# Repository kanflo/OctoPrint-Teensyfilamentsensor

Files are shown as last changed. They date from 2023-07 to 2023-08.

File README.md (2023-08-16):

# OctoPrint Teensy Filament Sensor

Work In Progress!

I wanted a filement sensor for my Duplicator 6 prompted by an "abnormal filament despooling incident". I found the "Smart Filament Sensor" by Bigtreetech, reasonably priced around 25 Euros, but it cannot be connected to the D6. I did have an old [Teensy 2.0](https://www.pjrc.com/teensy/) which could interface the filent sensor. An OctoPring plugin could then monitor the printing process, query the Teensy and act if the filament seemed to have run out or gotten jammed. Obviosly, this "Teensy Smart Filament Sensor" will work for any 3D printer.

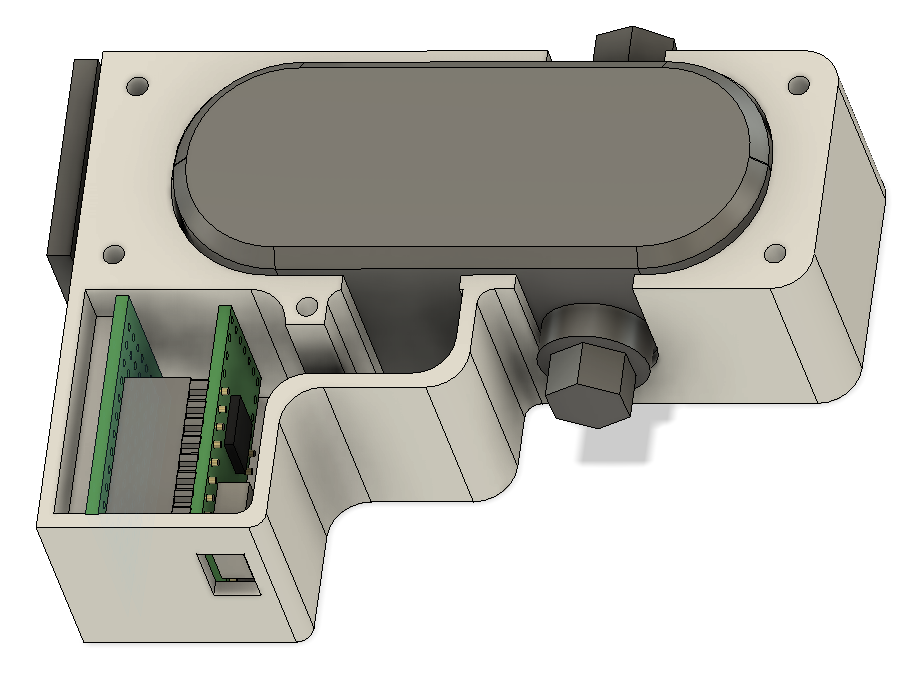
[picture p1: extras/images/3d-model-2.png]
3D Model


## Setup

Install via the bundled [Plugin Manager](https://docs.octoprint.org/en/master/bundledplugins/pluginmanager.html) or manually using this URL:

    https://github.com/kanflo/OctoPrint-Teensyfilamentsensor/archive/master.zip

## Teensy 2.0 firmware

The firmware for the Teensy implements a USB device talking RAW HID, meaning there is no need for a driver. Flash the Teensy with `filamentsensor.hex` or roll your own firmware.

## Mounting

I designed a housing the the filament sensor and Teensy that mounts nicely on the Duplicator 6. I printed them in PLA with 80% infill for sturdiness, probably overkill. Make sure you can insert the "lock peg" into the slot of the "back shell". Also "pre thread" all holes, especially the M4 holes in the lock peg and the corresponding holes in the back shell.

Material needed is:

 - 1x strip board, 9x11 holes
 - 2x Female headers 1x8 (or atleast 1x6)
 - 3x Male headers 1x1
 - 5x M3x8 screws
 - 2x M3 nuts
 - 2x M4x15 screws
 - 2x M4 nuts

1. First solder the headers to the strip board leaving one row of pins on the outside of the Teensy.
2. Solder three male single pin headers for VCC, GND and PF6.
3. Depending on you strip board, make sure the traces are cut, isolating the pins of the Teensy
4. The strip board is fastened by a pair of M3 screws and you need to drill holes in the strip board. Place in inside the 3D printed housing and mark the centers with a pen. Drill both holes.
5. Fasten the two M3 screws with a blob of hot glue or inserting the screw will be difficult. It should now look something like this:

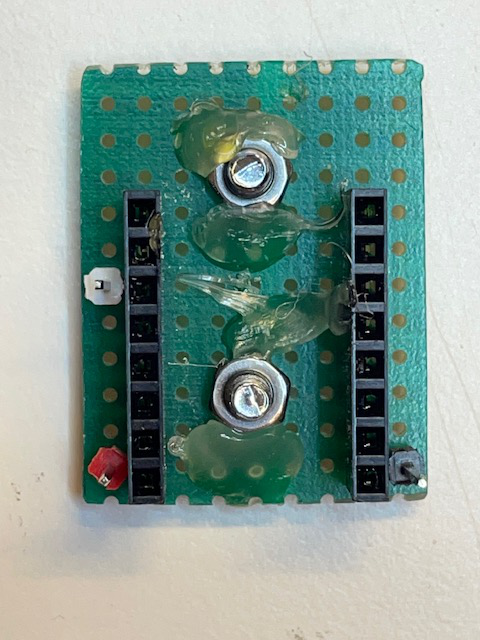
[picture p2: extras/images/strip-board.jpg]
Strip Board


6. Cut the wires fo the filament sensor to about 6cm in length and solder to the three headers. The wires on mine were marked with dense dots (VCC, red), stripes (GND, black) and sparse dots (S, white):

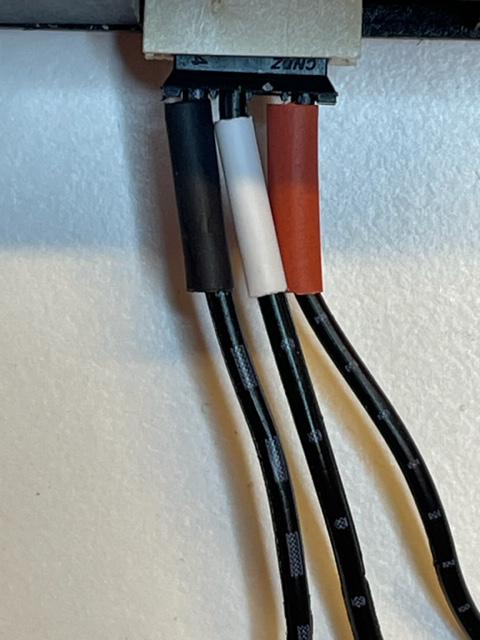
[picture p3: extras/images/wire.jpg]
Filament Sensor Wire


7. Connect the filament sensor to the Teensy, place everything in the housing:

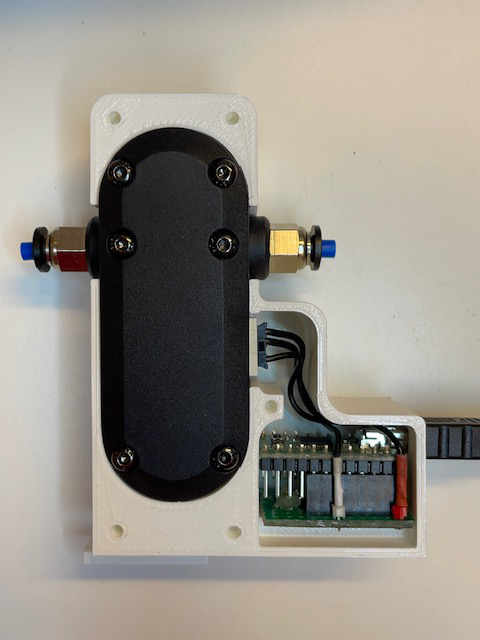
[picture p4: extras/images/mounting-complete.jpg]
Mounting Complete!


8. Depending on your filament sensor, you might need to crack it open and cut the spring inside. Mine was so stiff the extruder failed to pull the filament through the sensor. I took two pair of pliers and pulled the spring and then cut away pieces or it until it was looes enough. I am not sure if it helps, but this is the amount of material I removed:

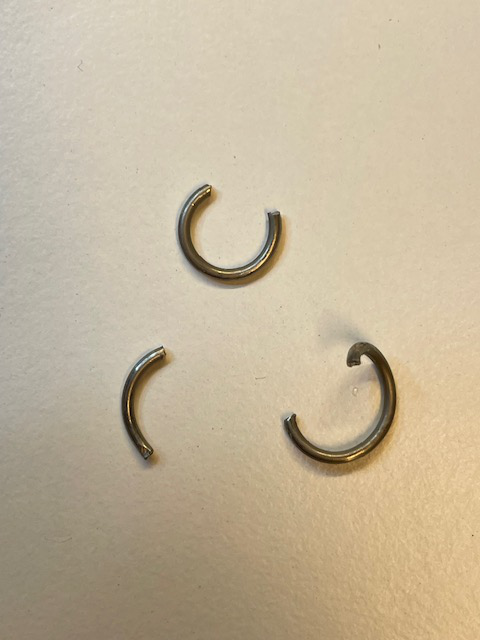
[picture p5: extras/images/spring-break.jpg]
Spring Break


9. Now it's time to mount the sensor. I removed the top holder for the extruder cable to gain access to the mounting hole:

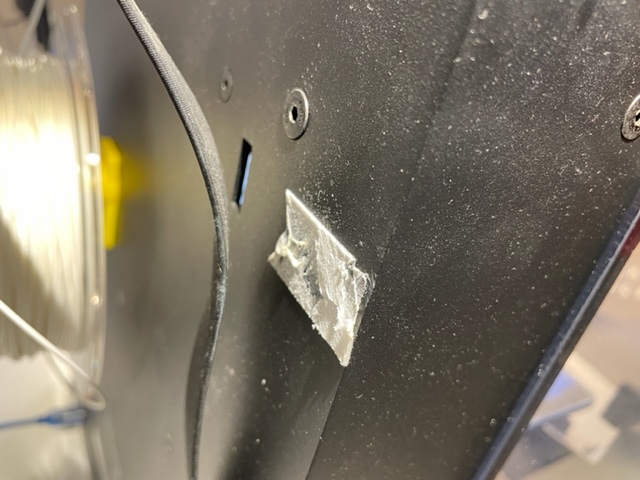
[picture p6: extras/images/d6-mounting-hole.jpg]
D6 Mounting Hole


10. Press the "lock peg" through the hole of the D6, press the housing with the sensor and everything against the lock peg and realize you need one more hand for fastening the M4 screws. I honestly have no idea how I did ut, but succeeded with only two hands ;)

11. Fasten the M4 screws. I had a bit of wiggle so I added some double sided tape between the D6 back wall and the housing.

12. Insert the filement tube into the top of the filement sensor and feed your filament through it:

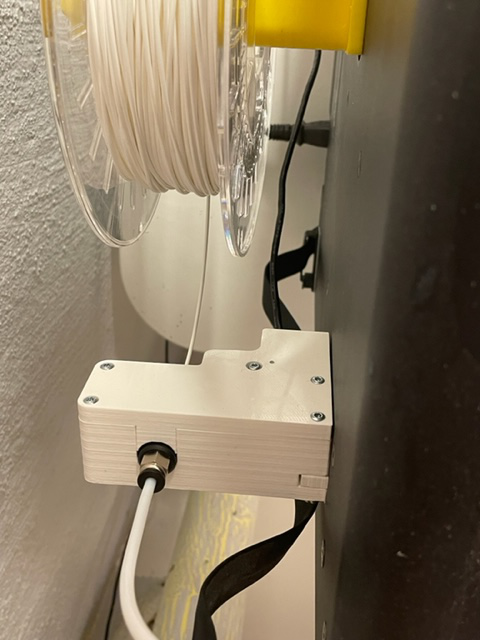
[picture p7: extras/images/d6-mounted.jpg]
Everything Mounted


## Using the filament sensor

Before using the sensor you need to copy a file to your OctoPrint installation. This requires that you know how to connect to your OctoPrint server using SSH:

```
scp extras/00-filament-sensor.rules octopi:
ssh octopi
sudo mv 00-filament-sensor.rules /etc/udev/rules.d
```

If you already connected the Teensy, disconnect and reconnect it.

The plugin adds a status icon to the top bar of the OctoPrint UI:

Filament status in OctoPrint

When the printer is idle, the icon will flash red/gray if the Teensy is disconnected and start flashing green/gray once the Teensy is connected. It should flash green/gray now. If not, ssh to your OctoPrint server and run the command `tail -f logs/octoprint.log`. The directory `logs` is located in a directory called `.octoprint` on my OctoPi.

When printing, the icon will be bright green when the filament status is ok. If the sensor detects a jam, it will light bright red and the print will be stopped (well, that's a TODO for now). If there is an error talking to the Teensy, or if the Teensy is disconnected when printing, the icon will flash bright red/gray.

When the counter ticks, the new counter will be written to the OctoPrint log.

## Configuration

Currently none.

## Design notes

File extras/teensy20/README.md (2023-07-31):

# Teensy 2.0 firmware for the filament sensor

For the impatient, flash `filementsensor.hex` to your Teensy 2.0 using the [https://www.pjrc.com/teensy/loader.html](Teensy loader). Any other Teensy will of course do, I used this 13 year little gem as I had one lying around. If you are patient, install `sudo apt install gcc-avr binutils-avr avr-libc` and run `make`.

Once flashed, you will see a RAW HID device with PID 0x04c9 and VID 0x1234 (I stole the PID from AT&T Microelectronics). Using RAW HID instead of a regular serial port makes you not connect OctoPrint to the filament sensor thinking it is your 3D printer ;)

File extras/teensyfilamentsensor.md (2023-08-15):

---
layout: plugin

id: teensyfilamentsensor
title: OctoPrint-Teensyfilamentsensor
description: A Teensy based filament sensor using Bigtreetech's 'Smart Filament Sensor'. Halts the print in case of filement runout or jam.
authors:
- Johan Kanflo
license: AGPLv3

# TODO
date: 2023-07-31

homepage: https://github.com/kanflo/OctoPrint-Teensyfilamentsensor
source: https://github.com/kanflo/OctoPrint-Teensyfilamentsensor
archive: https://github.com/kanflo/OctoPrint-Teensyfilamentsensor/archive/master.zip

# TODO
# Set this to true if your plugin uses the dependency_links setup parameter to include
# library versions not yet published on PyPi. SHOULD ONLY BE USED IF THERE IS NO OTHER OPTION!
#follow_dependency_links: false

# TODO
tags:
- filement
- sensor

# TODO
# When registering a plugin on plugins.octoprint.org, all screenshots should be uploaded not linked from external sites.
screenshots:
- url: extras/images/octoprint-status.png
  alt: OctoPrint Filement Status
  caption: OctoPrint Filement Status

featuredimage: /extras/images/smart-filament-sensor.png

# TODO
# You only need the following if your plugin requires specific OctoPrint versions or
# specific operating systems to function - you can safely remove the whole
# "compatibility" block if this is not the case.

compatibility:

  # List of compatible versions
  #
  # A single version number will be interpretated as a minimum version requirement,
  # e.g. "1.3.1" will show the plugin as compatible to OctoPrint versions 1.3.1 and up.
  # More sophisticated version requirements can be modelled too by using PEP440
  # compatible version specifiers.
  #
  # You can also remove the whole "octoprint" block. Removing it will default to all
  # OctoPrint versions being supported.

  octoprint:
  - 1.4.0

  # List of compatible operating systems
  #
  # Valid values:
  #
  # - windows
  # - linux
  # - macos
  # - freebsd
  #
  # There are also two OS groups defined that get expanded on usage:
  #
  # - posix: linux, macos and freebsd
  # - nix: linux and freebsd
  #
  # You can also remove the whole "os" block. Removing it will default to all
  # operating systems being supported.

  os:
  - linux
  - windows
  - macos
  - freebsd

  # Compatible Python version
  #
  # It is recommended to only support Python 3 for new plugins, in which case this should be ">=3,<4"
  #
  # Plugins that wish to support both Python 2 and 3 should set it to ">=2.7,<4".
  #
  # Plugins that only support Python 2 will not be accepted into the plugin repository.

  python: ">=3,<4"

---

This is a plugin that talks to a microcontroller interfacing a "Smart Filament Sensor" from Bigtreetech. Currently a Teensy 2.0 is used but any microcontroller will do. The result is a filement sensor that works on any 3D printer.

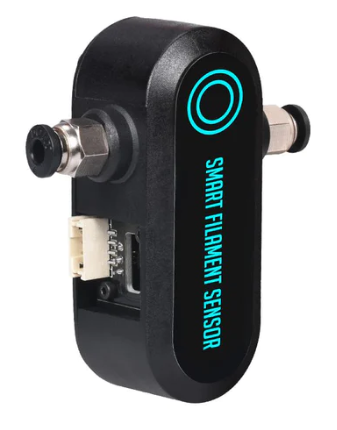
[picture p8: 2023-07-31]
extras/images/smart-filament-sensor.png

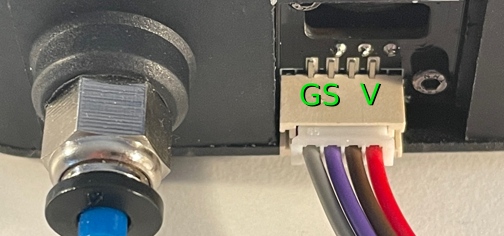
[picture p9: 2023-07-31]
extras/images/smart-filement-sensor-pinut.png

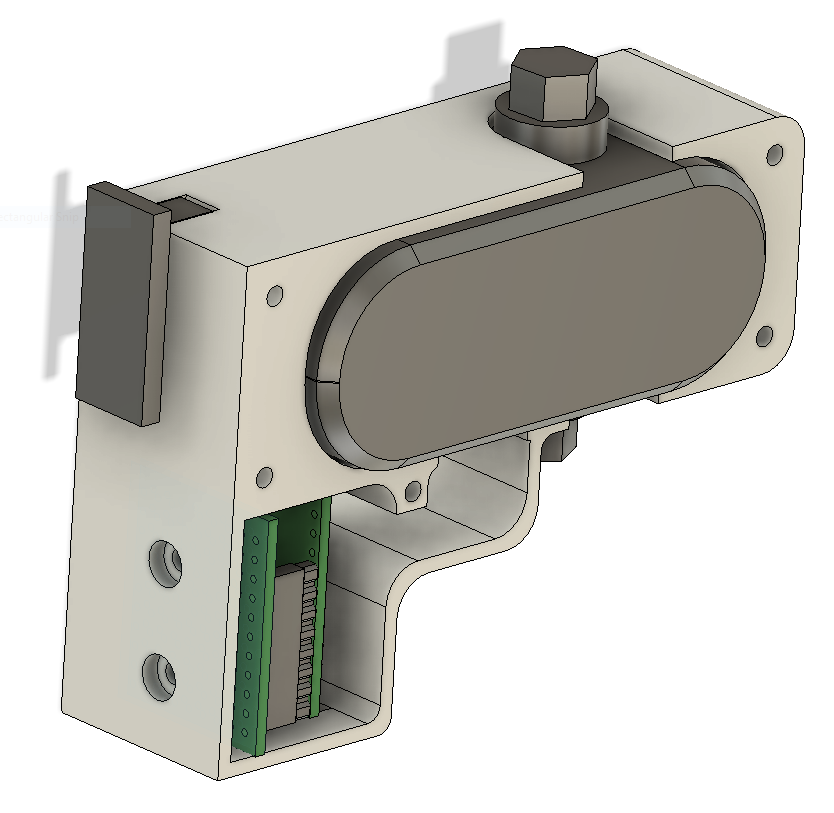
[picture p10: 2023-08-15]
extras/images/3d-model-1.png

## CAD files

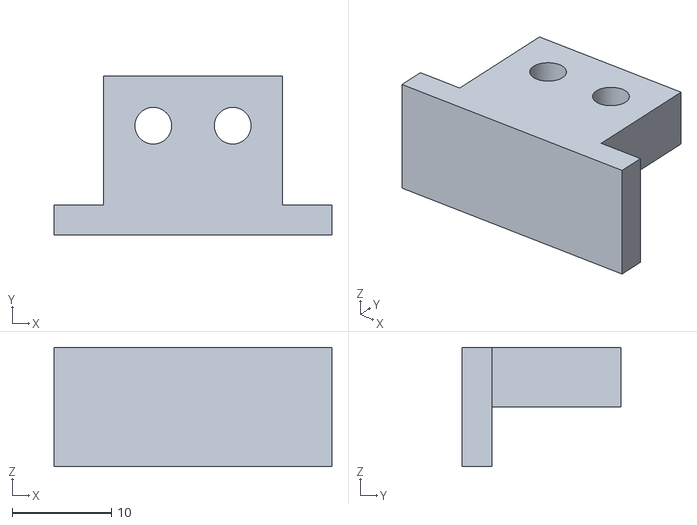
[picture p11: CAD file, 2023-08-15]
extras/stl/Lock Peg v5.stl
28.0 x 16.0 x 12.0

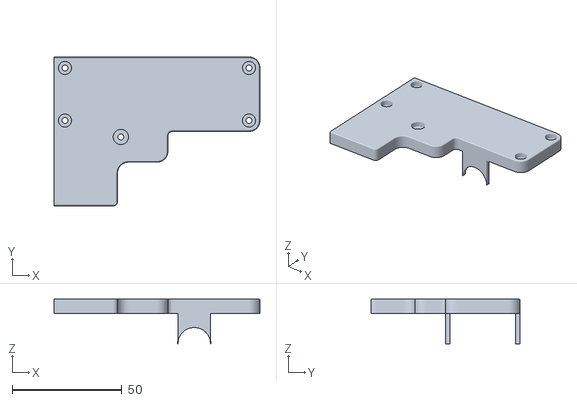
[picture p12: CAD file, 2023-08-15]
extras/stl/Top Shell v19.stl
94.0 x 68.0 x 20.5

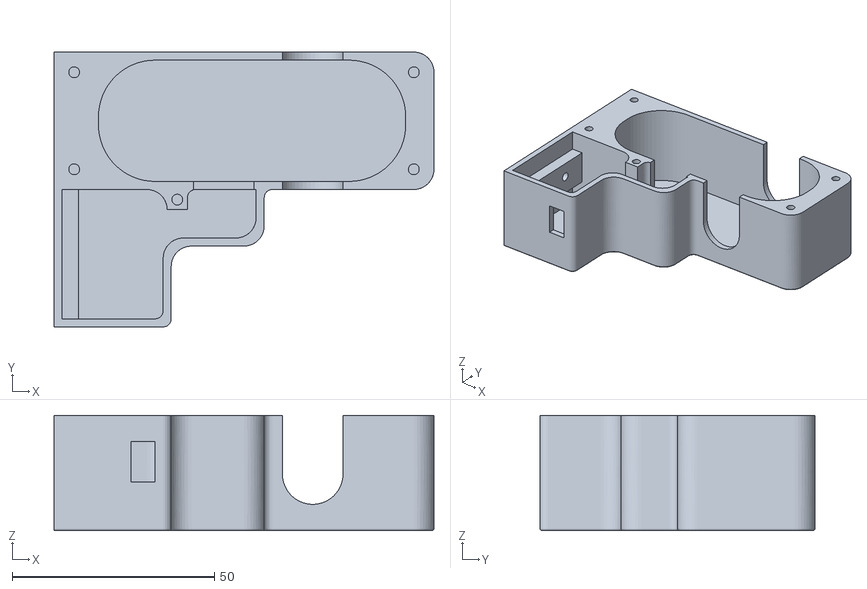
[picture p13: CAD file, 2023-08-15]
extras/stl/Back Shell v26.stl
94.0 x 68.0 x 28.5

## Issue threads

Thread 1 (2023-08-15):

Implement printer stop

kanflo, 2023-08-15:
Currently, the plugin only logs the sensor counter at start of printing and when printing finishes. Investigate how much (or little) filament move is considered normal and implement print stop.

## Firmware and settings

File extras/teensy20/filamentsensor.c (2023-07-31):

/*
 * Copyright (c) 2023 Johan Kanflo
 * https://github.com/kanflo
 *
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
 * The above description, website URL and copyright notice and this permission
 * notice shall be included in all copies or substantial portions of the Software.
 *
 * THE SOFTWARE IS PROVIDED "AS IS", WITHOUT WARRANTY OF ANY KIND, EXPRESS OR
 * IMPLIED, INCLUDING BUT NOT LIMITED TO THE WARRANTIES OF MERCHANTABILITY,
 * FITNESS FOR A PARTICULAR PURPOSE AND NONINFRINGEMENT. IN NO EVENT SHALL THE
 * AUTHORS OR COPYRIGHT HOLDERS BE LIABLE FOR ANY CLAIM, DAMAGES OR OTHER
 * LIABILITY, WHETHER IN AN ACTION OF CONTRACT, TORT OR OTHERWISE, ARISING FROM,
 * OUT OF OR IN CONNECTION WITH THE SOFTWARE OR THE USE OR OTHER DEALINGS IN
 * THE SOFTWARE.
 */

#include <avr/io.h>
#include <avr/pgmspace.h>
#include <avr/interrupt.h>
#include <util/delay.h>
#include <string.h>
#include "usb_rawhid.h"
#include "common.h"

#define CPU_PRESCALE(n)	(CLKPR = 0x80, CLKPR = (n))

#define LED_PIN     (6)
#define SENSOR_PIN  (6)

// Is it time to send a packet to the host?
volatile bool g_do_output = false;
// Number of filement sensor pulses we have detected
volatile uint32_t g_filament_counter = 0;
// Current pin level
volatile bool g_filament_pin_level = 0;


static void set_led(bool on)
{
	if (on) {
		PORTD |= 1 << LED_PIN;
	} else {
		PORTD &= ~(1 << LED_PIN);
	}
}

static bool get_filament_pin_level(void)
{
	return PINF & (1 << SENSOR_PIN) ? true : false;
}

// Set the LED
static void handle_led_command(uint32_t state)
{
	switch (state) {
		case LED_ON:
			set_led(true);
			break;
		case LED_OFF:
			set_led(false);
			break;
	}
}

// Reset the device into the boot loader (halfkay).
// This is handy if you embed the Teensy and cannot reach the reset button.
static void handle_reset_command(void)
{
	cli();
	// Disable watchdog, if enabled
	// Disable all peripherals
	UDCON = 1;
	USBCON = (1 << FRZCLK);  // Disable USB
	UCSR1B = 0;
	_delay_ms(5);
#if defined(__AVR_AT90USB162__)                // Teensy 1.0
    DDRB = 0; DDRC = 0; DDRD = 0;
    TIMSK0 = 0; TIMSK1 = 0;
    asm volatile("jmp 0x1F00");
#elif defined(__AVR_ATmega32U4__)              // Teensy 2.0
    DDRB = 0; DDRC = 0; DDRD = 0; DDRE = 0; DDRF = 0;
    TIMSK0 = 0; TIMSK1 = 0; TIMSK3 = 0; TIMSK4 = 0;
    ADCSRA = 0;
    asm volatile("jmp 0x3F00");
#elif defined(__AVR_AT90USB646__)              // Teensy++ 1.0
    DDRA = 0; DDRB = 0; DDRC = 0; DDRD = 0; DDRE = 0; DDRF = 0;
    TIMSK0 = 0; TIMSK1 = 0; TIMSK2 = 0; TIMSK3 = 0;
    ADCSRA = 0;
    asm volatile("jmp 0x7E00");
#elif defined(__AVR_AT90USB1286__)             // Teensy++ 2.0
    DDRA = 0; DDRB = 0; DDRC = 0; DDRD = 0; DDRE = 0; DDRF = 0;
    TIMSK0 = 0; TIMSK1 = 0; TIMSK2 = 0; TIMSK3 = 0;
    ADCSRA = 0;
    asm volatile("jmp 0xFE00");
#else
 #error "Unknown board"
#endif
}

// Parse a packet sent from the host
static void parse_out_packet(uint8_t *buf, uint8_t len)
{
	if(packet_ok(buf, len)) {
		uint32_t data = ((uint32_t) (buf[PACKET_DATA_POS])   << 24) |
		                ((uint32_t) (buf[PACKET_DATA_POS+1]) << 16) |
						(buf[PACKET_DATA_POS+2] <<  8) |
						buf[PACKET_DATA_POS+3];
		switch(buf[PACKET_CMD_POS]) {
			case CMD_RESET_COUNTER:
				g_filament_counter = 0;
				handle_led_command(0);
				break;
			case CMD_LED:
				handle_led_command(data);
				break;
			case CMD_RESET:
				handle_reset_command();
				break;
		}
	} else {
		// Not a whole lot we can do.
	}
}

// Main program
int main(void)
{
	int8_t r;
	uint8_t buffer[PACKET_SIZE];

	// Set for 16 MHz clock
	CPU_PRESCALE(0);

	// The on board LED is connected to PD6
	DDRD |= 1 << LED_PIN;
	set_led(true);

    // Filament sensor is connected to PF6
    DDRF &= ~(1 << SENSOR_PIN);
    // Enable pull up to eliminate flutter in case the sensor is disconnected
    PORTF |= 1 << SENSOR_PIN;
    g_filament_pin_level = get_filament_pin_level();

	// Initialize the USB, and then wait for the host to set configuration.
	// If the Teensy is powered without a PC connected to the USB port,
	// this will wait forever.
	usb_init();
	while (!usb_configured()) /* wait */ ;

	// Wait an extra second for the PC's operating system to load drivers
	// and do whatever it does to actually be ready for input
	_delay_ms(1000);

    // Configure timer 0 to generate a timer overflow interrupt every
    // 256*1024 clock cycles, or approx 61 Hz when using 16 MHz clock
    TCCR0A = 0x00;
    TCCR0B = 0x05;
    TIMSK0 = (1 << TOIE0);

	while (1) {
        if (g_filament_pin_level != get_filament_pin_level()) {
            g_filament_pin_level = get_filament_pin_level();
            g_filament_counter++;
            set_led(g_filament_pin_level);
        }

		r = usb_rawhid_recv(buffer, 0);
		if (r > 0) {
			parse_out_packet((uint8_t*) buffer, (uint8_t) r);
		}
		// Time to send filament counter
		if (g_do_output) {
			g_do_output = false;
			build_packet((uint8_t*) buffer, CMD_COUNTER, g_filament_counter);
			usb_rawhid_send(buffer, 50);
		}
	}
}

// This interrupt routine is run approx 61 times per second.
ISR(TIMER0_OVF_vect)
{
	static uint8_t output_count = 0;
	// Set the g_do_output variable every ~0.5 seconds
	if (output_count++ > 30) {
		output_count = 0;
		g_do_output = true;
	}
}
